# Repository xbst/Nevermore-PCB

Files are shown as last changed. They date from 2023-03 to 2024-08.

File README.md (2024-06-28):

# Nevermore Mini, Max & Stealthmax PCBs
| Nevermore Max 2 PCB | Nevermore Mini & Stealthmax PCB | Nevermore Stealthmax PCB 2|
| --- | --- | --- |
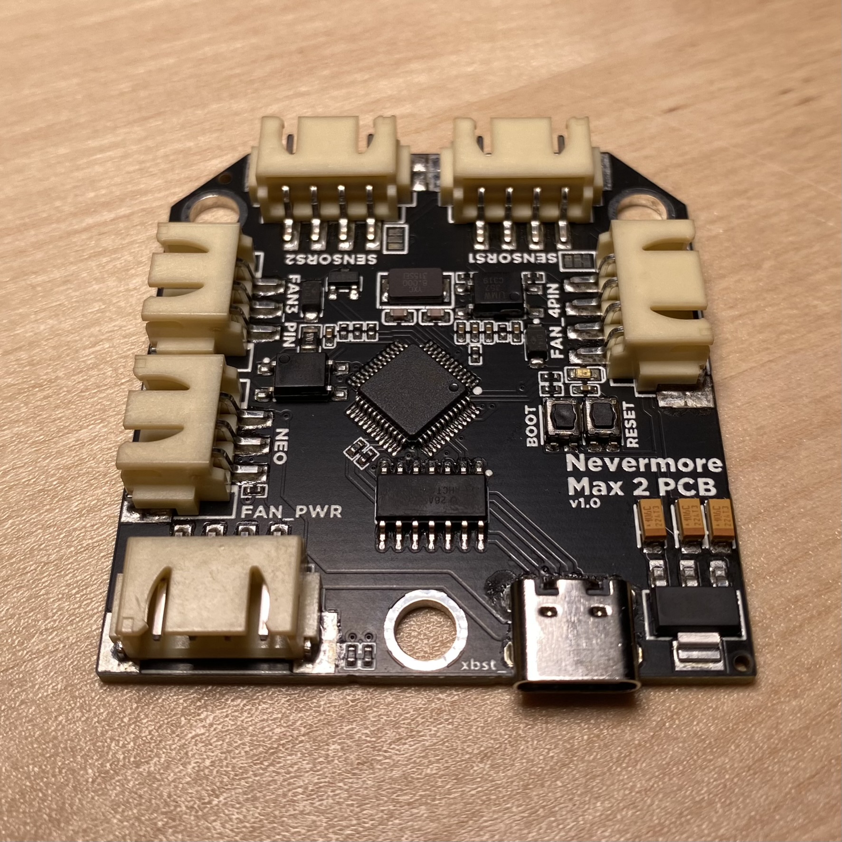
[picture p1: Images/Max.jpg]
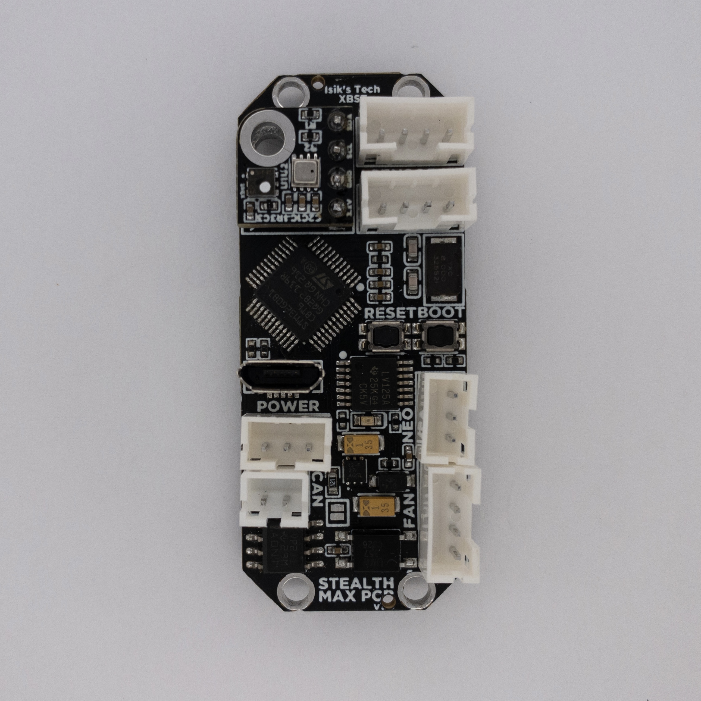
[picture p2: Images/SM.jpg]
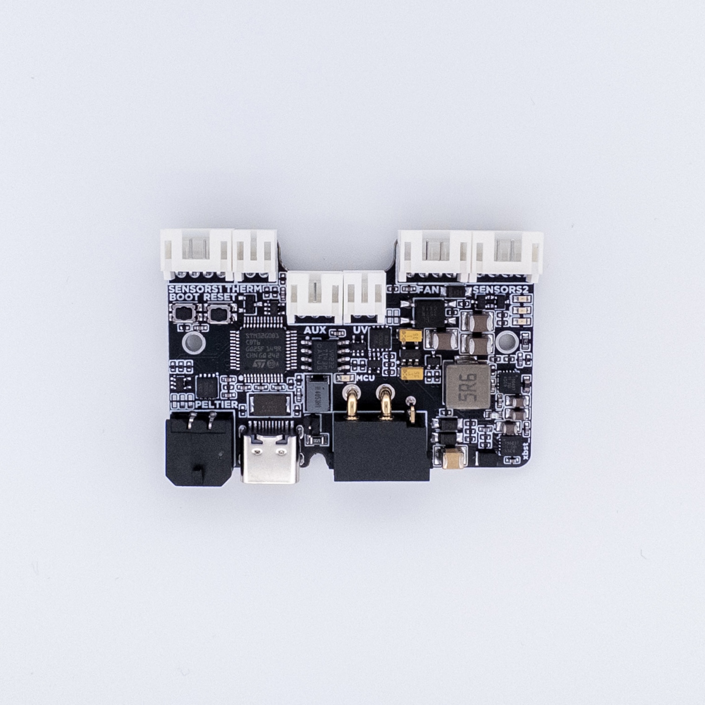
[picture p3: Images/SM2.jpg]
||||

<br>PCBs for Nevermore Mini, Nevermore Max and Nevermore Stealthmax air filters. 
<br>More information about the Nevermore Max 2 air filter can be found [here](https://github.com/nevermore3d/Nevermore_Max)
<br>More information about the Nevermore Stealthmax air filter can be found [here](https://github.com/nevermore3d/StealthMax)
<br>More information about the Nevermore Mini air filter can be found [here](https://www.printables.com/model/757663-nevermore-mini-3d-printer-hepa-and-carbon-air-filt).

### Features
|| Nevermore Max 2 PCB | Nevermore Mini & Stealthmax PCB | Nevermore Stealthmax PCB 2|
|---|---|---|---|
|||||
|MCU|STM32G0B1 MCU|STM32G0B1 MCU|STM32G0B1 MCU|
|Fans|1x 4-pin, 1x 3/2-pin|1x4-pin|1x4-pin|
|Sensors|2x HW I2C|2x HW I2C, 1x Optional Sensor Module Mount|2x HW I2C|
|Neopixels|1x Neopixel|1x Neopixel|-|
|CAN Bus|-|Yes, 1M|Yes, 1M|
|12V Regulator|-|-|Yes, Max. 12V@5A, From 24V|
|5V Regulator|-|-|Yes, From 24V, Turns Off w/ USB to Use USB 5V|
|3.3V Regulator|Yes, From 5V|Yes, From 5V|Yes, From 5V|
|UV LED Control|-|-|1x MOSFET, 1x PWM|
|Peltier Control|-|-|1x MOSFET|
|Thermistors|-|-|1x On-PCB 3950, 1x Connector|
|Connectors|JST-XH, USB C|JST-PH, USB Micro-B|JST-PH, USB C, XT30(2+2), MX3.0 (for Peltier)|

## Purchasing a Nevermore PCB
### United States
|Store|Max|Mini & Stealthmax|Stealthmax 2|
|---|---|---|---|
|Isik's Tech (Me)|[PCB](https://store.isiks.tech/products/nevermore-max-controller-pcb)<br>[Bundle](https://store.isiks.tech/products/nevermore-max-bundle)|[PCB](https://store.isiks.tech/products/nevermore-stealthmax-pxb)<br>[Bundle](https://store.isiks.tech/products/nevermore-stealthmax-bundle)|[PCB](https://store.isiks.tech/products/nevermore-stealthmax-2-pcb)<br>[Bundle](https://store.isiks.tech/products/nevermore-stealthmax-2-bundle)|
|XR Bunker|[PCB](https://xrbunker.works/products/nevermore-max-2-red-pcb-by-xbst_isik)|-|-|

This project is licensed under [GPL v3](./LICENSE), meaning vendors are allowed to sell PCBs without paying me. If you'd like to support the development of this and future projects please consider [sponsoring](https://github.com/sponsors/xbst) me on GitHub. You can also subscribe on [Patreon](https://l.isiks.tech/patreon) or [YouTube](https://l.isiks.tech/member).

You can also use the included gerber files to order your own from a PCB manufacturer like [PCBWay](https://www.pcbway.com/setinvite.aspx?inviteid=374841) or [JLCPCB](https://jlcpcb.com/).
<br>

## Instructions
- [Nevermore Max PCB](./Docs/Max.md)
- [Nevermore Mini & Stealthmax PCB](./Docs/SM.md)
- [Nevermore Stealthmax PCB 2](./Docs/SM2.md)

## YouTube

I am a YouTube content creator. If you want content about these projects & more, please consider [subscribing to my YouTube channel](https://www.youtube.com/channel/UClAWYmCkHjsbaX9Wz1df2mg).
<br>

If you feel like contributing to the development of this project and other projects like this you can sponsor me on [GitHub](https://github.com/sponsors/xbst), subscribe on [Patreon](https://l.isiks.tech/patreon) or [YouTube](https://l.isiks.tech/member).

## Notes
- This readme file contains affiliate links. I make a comission on qualifying purchases.
- This project does not come with any warranty, if you choose to build/use a Nevermore PCB, you are doing this at your own risk!
- If you want to sell PCBs, you are allowed to, and you will not owe me any royalties. **You cannot claim that I endorse the sale**. You can check the license file for more information. However, if you **wish** to give me a share you can sponsor me on [GitHub](https://github.com/sponsors/xbst), subscribe on [Patreon](https://l.isiks.tech/patreon) or [YouTube](https://l.isiks.tech/member).

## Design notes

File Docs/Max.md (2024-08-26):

# Nevermore Max 2 PCB Instructions

## Firmware Flashing

:warning: Do not skip steps 1-6 if you sourced your PCB from anywhere but Isik's Tech. If you do and this setting wasn't pre-applied by the vendor you purchased from, you won't be able to reflash firmware after the initial flash.

1. SSH into your Raspberry Pi.
2. Download the STM32G0 legacy nBOOT_SEL setting file from [its repo](https://github.com/olikraus/stm32g031/tree/main/enable_boot0).  `sudo wget https://raw.githubusercontent.com/olikraus/stm32g031/main/enable_boot0/enable_boot0.hex`
3. Convert the hex file you downloaded to binary. `objcopy --input-target=ihex --output-target=binary enable_boot0.hex enable_boot0.bin`
4. Connect your Nevermore Max PCB to your Raspberry Pi while holding down the `BOOT` button.
5. Use `lsusb` to make sure you can see the device in DFU mode.
6. Flash the binary file to enable legacy nBOOT_SEL mode. `sudo dfu-util -a 0 -d 0483:df11 --dfuse-address 0x08000000:leave -D enable_boot0.bin`
7. Hold down the `BOOT` button on your PCB. While holding it down, press `RESET`, then release `BOOT`. Alternatively, you can unplug the PCB then plug it in again while holding down the `BOOT` button. Use `lsusb` again to make sure you can see the device in DFU mode
8. Go to the Klipper directory. `cd klipper`
9. Clean remaining files from previous build. `make clean`
10. Choose the options for the build. `make menuconfig` Use the following options:
```
[*] Enable extra low-level configuration options
    Micro-controller Architecture (STMicroelectronics STM32)  --->
    Processor model (STM32G0B1)  --->
    Bootloader offset (No bootloader)  --->
    Clock Reference (8 MHz crystal)  --->
    Communication interface (USB (on PA11/PA12))  --->
    USB ids  --->
()  GPIO pins to set at micro-controller startup
```
Press `Q` then `Y` to save and quit the menu.

11. Build. `make`
12. Flash. `make flash FLASH_DEVICE=0483:df11`
13. When finished, press the `RESET` button on your Nevermore Max PCB.
14. Use  `ls /dev/serial/by-id/*` to find the path starting with `/dev/serial/by-id/usb-Klipper_stm32g0b1`. This is the serial path of your Nevermore Max PCB.
15. While you're SSH'd in, also download the python code needed for the SGP40 sensors from the [Nevermore Max repo](https://github.com/nevermore3d/Nevermore_Max).
```
wget https://raw.githubusercontent.com/nevermore3d/Nevermore_Max/master/Software/Klipper/sgp40.py -P ~/klipper/klippy/extras
wget https://raw.githubusercontent.com/nevermore3d/Nevermore_Max/master/Software/Klipper/voc_algorithm.py -P ~/klipper/klippy/extras
systemctl restart klipper
```
16. Run this command if you are using Mainsail and want the SGP40s displayed on the dashboard:
```
cd ~/mainsail/ && grep -l additionalSensors * -R | xargs sed -i 's+additionalSensors=\[+additionalSensors=\["sgp40",+g'
```

## PCB Mount & Wiring
1. Print the ~~bottle opener~~ [Nevermore Max PCB tray](../Mounts/Max/PCB-Tray.stl) using the standard Voron print settings.
2. Remove the built-in supports.
3. Superglue 2 magnets. Pay attention to the polarities.
4. Mount the PCB. The plastic latches will keep the PCB in place, no screws needed. The USB/power side should be seated first.
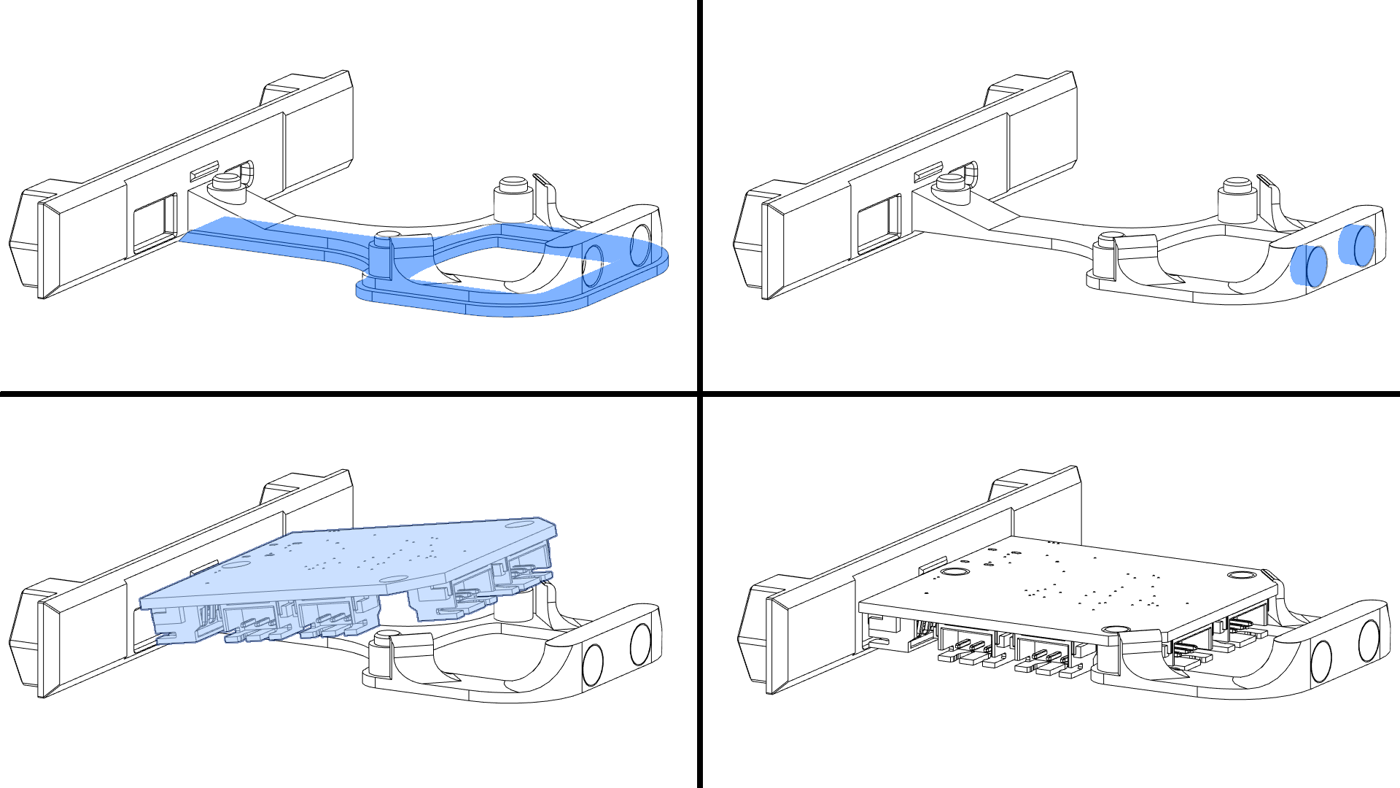
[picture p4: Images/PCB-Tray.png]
Instructions

5. All connectors except USB are JST-XH. Use the diagram below to wire your fans/sensors/leds/power.
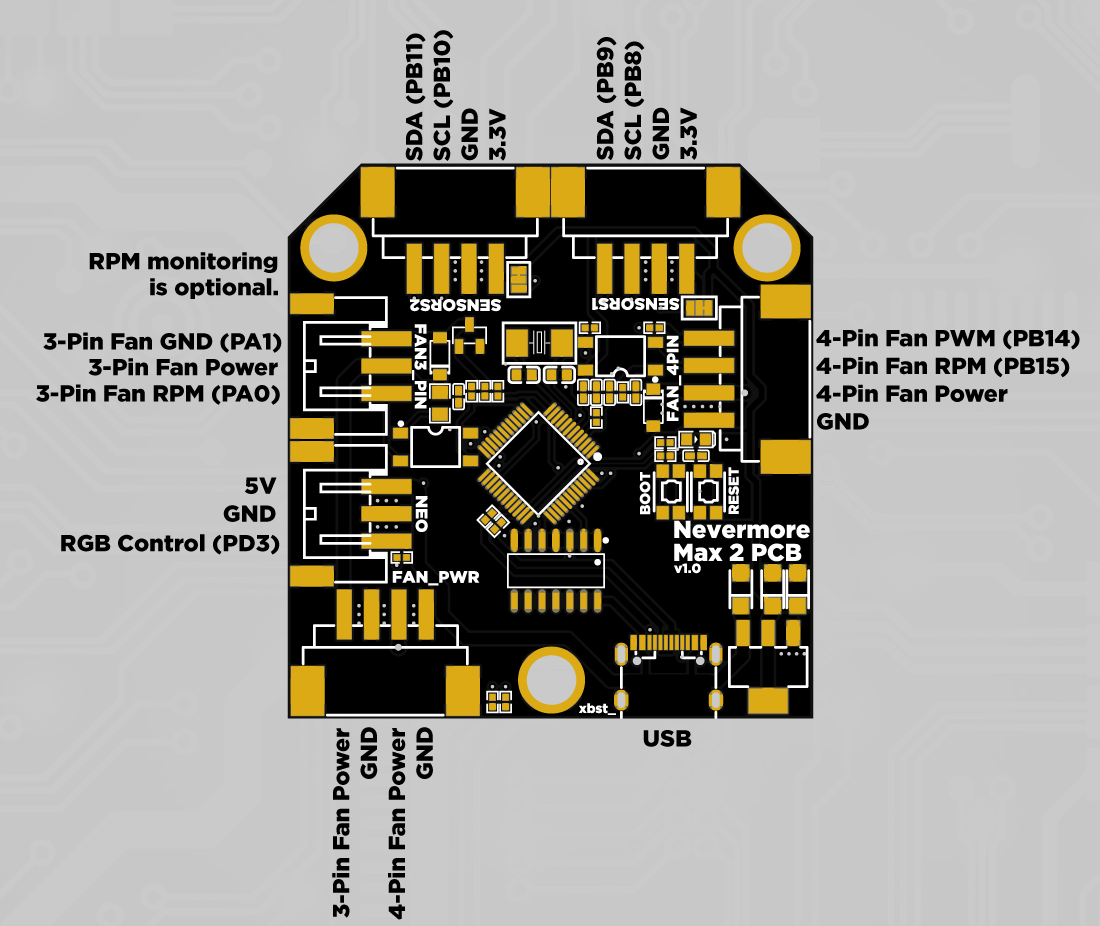
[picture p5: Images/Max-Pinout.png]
Pinout


## Klipper Config
1. Download the [Klipper config](../Firmware/Max.cfg), and upload it to your printer.
2. Open the file and edit according to your setup.
3. Add `[include max.cfg]` in your `printer.cfg`.

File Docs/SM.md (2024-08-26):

# Nevermore Mini And Stealthmax PCB Instructions

## Firmware Flashing

:warning: Do not skip steps 1-6 if you sourced your PCB from anywhere but Isik's Tech. If you do and this setting wasn't pre-applied by the vendor you purchased from, you won't be able to reflash firmware after the initial flash.

1. SSH into your Raspberry Pi.
2. Download the STM32G0 legacy nBOOT_SEL setting file from [its repo](https://github.com/olikraus/stm32g031/tree/main/enable_boot0).  `sudo wget https://raw.githubusercontent.com/olikraus/stm32g031/main/enable_boot0/enable_boot0.hex`
3. Convert the hex file you downloaded to binary. `objcopy --input-target=ihex --output-target=binary enable_boot0.hex enable_boot0.bin`
4. Connect your Nevermore Stealthmax PCB to your Raspberry Pi while holding down the `BOOT` button.
5. Use `lsusb` to make sure you can see the device in DFU mode.
6. Flash the binary file to enable legacy nBOOT_SEL mode. `sudo dfu-util -a 0 -d 0483:df11 --dfuse-address 0x08000000:leave -D enable_boot0.bin`
7. Hold down the `BOOT` button on your PCB. While holding it down, press `RESET`, then release `BOOT`. Alternatively, you can unplug the PCB then plug it in again while holding down the `BOOT` button. Use `lsusb` again to make sure you can see the device in DFU mode
8. Go to the Klipper directory. `cd klipper`
9. Clean remaining files from previous build. `make clean`
10. Choose the options for the build. `make menuconfig` Use the following options:

<details>
  <summary>For USB Serial Communication</summary>

```
[*] Enable extra low-level configuration options
    Micro-controller Architecture (STMicroelectronics STM32)  --->
    Processor model (STM32G0B1)  --->
    Bootloader offset (No bootloader)  --->
    Clock Reference (8 MHz crystal)  --->
    Communication interface (USB (on PA11/PA12))  --->
    USB ids  --->
()  GPIO pins to set at micro-controller startup
```

</details>
<details>
  <summary>For CAN Bus Communication WITHOUT Katapult</summary>

```
[*] Enable extra low-level configuration options
    Micro-controller Architecture (STMicroelectronics STM32)  --->
    Processor model (STM32G0B1)  --->
    Bootloader offset (No bootloader)  --->
    Clock Reference (8 MHz crystal)  --->
    Communication interface (CAN bus (on PB0/PB1))  --->
(1000000) CAN bus speed
()  GPIO pins to set at micro-controller startup
```

</details>
<details>
  <summary>For CAN Bus Communication WITH Katapult</summary>

```
[*] Enable extra low-level configuration options
    Micro-controller Architecture (STMicroelectronics STM32)  --->
    Processor model (STM32G0B1)  --->
    Bootloader offset (8KiB Bootloader)  --->
    Clock Reference (8 MHz crystal)  --->
    Communication interface (CAN bus (on PB0/PB1))  --->
(1000000) CAN bus speed
()  GPIO pins to set at micro-controller startup
```

</details>

Press `Q` then `Y` to save and quit the menu.

11. Build. `make`
12. Flash the firmware. 
<details>
  <summary>For USB Serial Communication</summary>
  
  1. Flash Klipper. `make flash FLASH_DEVICE=0483:df11`
  2. When finished, press the `RESET` button on your Nevermore Stealthmax PCB.
  3. Use  `ls /dev/serial/by-id/*` to find the path starting with `/dev/serial/by-id/usb-Klipper_stm32g0b1`. This is the serial path of your Nevermore Stealthmax PCB.
  
</details>
<details>
  <summary>For CAN Bus Communication WITHOUT Katapult</summary>
  
  1. Flash Klipper. `make flash FLASH_DEVICE=0483:df11`
  2. When finished, press the `RESET` button on your Nevermore Stealthmax PCB.
  3. Use  `~/klippy-env/bin/python ~/klipper/scripts/canbus_query.py can0` to find the CAN bus UUID of your Nevermore Stealthmax PCB. (Make sure your CAN wires are connected.)

</details>
<details>
  <summary>For CAN Bus Communication WITH Katapult</summary>

  1. Go home. `cd ~`
  2. Install [Katapult](https://github.com/Arksine/katapult). `git clone https://github.com/Arksine/katapult`
  3. Go to the Katapult directory. `cd katapult`
  4. Choose the options for the build. `make menuconfig` Use the following options:
    
  ```
    Micro-controller Architecture (STMicroelectronics STM32)  --->
    Processor model (STM32G0B1)  --->
    Build Katapult deployment application (Do not build)  --->
    Clock Reference (8 MHz crystal)  --->
    Communication interface (CAN bus (on PB0/PB1))  --->
    Application start offset (8KiB offset)  --->
(1000000) CAN bus speed
()  GPIO pins to set on bootloader entry
[*] Support bootloader entry on rapid double click of reset button
[ ] Enable bootloader entry on button (or gpio) state
[*] Enable Status LED
(PA13)  Status LED GPIO Pin
  ```
5. Build. `make`
6. Flash Katapult. `sudo dfu-util -a 0 -d 0483:df11 --dfuse-address 0x08000000:leave -D out/canboot.bin`
7. When finished, press the `RESET` button on your Nevermore Stealthmax PCB.
8. Use  `~/klippy-env/bin/python ~/klipper/scripts/canbus_query.py can0` to find the CAN bus UUID of your Nevermore Stealthmax PCB. (Make sure your CAN wires are connected.)
9. Flash Klipper. Replace `<UUID>` with your PCB's UUID. `cd ~/katapult/scripts && python3 flashtool.py -i can0 -f ~/klipper/out/klipper.bin -u <uuid>`
10. When finished, press the `RESET` button on your Nevermore Stealthmax PCB.

</details>

13. While you're SSH'd in, also download the python code needed for the SGP40 sensors from the [Nevermore Max repo](https://github.com/nevermore3d/Nevermore_Max).
```
wget https://raw.githubusercontent.com/nevermore3d/Nevermore_Max/master/Software/Klipper/sgp40.py -P ~/klipper/klippy/extras
wget https://raw.githubusercontent.com/nevermore3d/Nevermore_Max/master/Software/Klipper/voc_algorithm.py -P ~/klipper/klippy/extras
systemctl restart klipper
```
14. Run this command if you are using Mainsail and want the SGP40s displayed on the dashboard:
```
cd ~/mainsail/ && grep -l additionalSensors * -R | xargs sed -i 's+additionalSensors=\[+additionalSensors=\["sgp40",+g'
```

## PCB Mount & Wiring
1. Mount the PCB where the Raspberry Pi Pico normally mounts with M2 screws.
2. All connectors except USB are JST-PH. Use the diagram below to wire your fans/sensors/CAN/power.
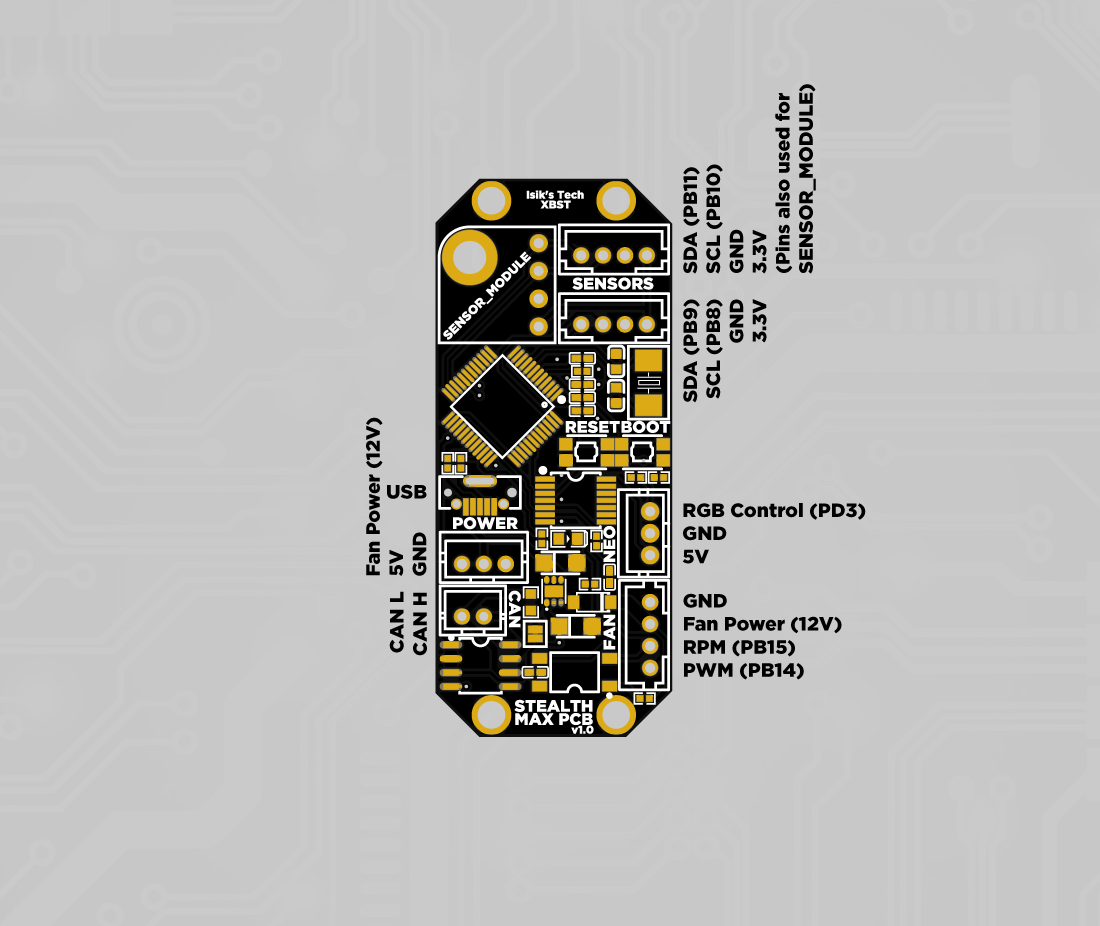
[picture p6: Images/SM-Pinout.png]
Pinout


## Klipper Config
1. Download the [Klipper config](../Firmware/Max.cfg), and upload it to your printer.
2. Open the file and edit according to your setup.
3. Add `[include max.cfg]` in your `printer.cfg`.

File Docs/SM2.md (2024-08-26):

# Nevermore Stealthmax PCB 2 Instructions

## Firmware Flashing

:warning: Do not skip steps 1-6 if you sourced your PCB from anywhere but Isik's Tech. If you do and this setting wasn't pre-applied by the vendor you purchased from, you won't be able to reflash firmware after the initial flash.

1. SSH into your Raspberry Pi.
2. Download the STM32G0 legacy nBOOT_SEL setting file from [its repo](https://github.com/olikraus/stm32g031/tree/main/enable_boot0).  `sudo wget https://raw.githubusercontent.com/olikraus/stm32g031/main/enable_boot0/enable_boot0.hex`
3. Convert the hex file you downloaded to binary. `objcopy --input-target=ihex --output-target=binary enable_boot0.hex enable_boot0.bin`
4. Connect your Nevermore Stealthmax PCB to your Raspberry Pi while holding down the `BOOT` button.
5. Use `lsusb` to make sure you can see the device in DFU mode.
6. Flash the binary file to enable legacy nBOOT_SEL mode. `sudo dfu-util -a 0 -d 0483:df11 --dfuse-address 0x08000000:leave -D enable_boot0.bin`
7. Hold down the `BOOT` button on your PCB. While holding it down, press `RESET`, then release `BOOT`. Alternatively, you can unplug the PCB then plug it in again while holding down the `BOOT` button. Use `lsusb` again to make sure you can see the device in DFU mode
8. Go to the Klipper directory. `cd klipper`
9. Clean remaining files from previous build. `make clean`
10. Choose the options for the build. `make menuconfig` Use the following options:

<details>
  <summary>For USB Serial Communication</summary>

```
[*] Enable extra low-level configuration options
    Micro-controller Architecture (STMicroelectronics STM32)  --->
    Processor model (STM32G0B1)  --->
    Bootloader offset (No bootloader)  --->
    Clock Reference (8 MHz crystal)  --->
    Communication interface (USB (on PA11/PA12))  --->
    USB ids  --->
()  GPIO pins to set at micro-controller startup
```

</details>
<details>
  <summary>For CAN Bus Communication WITHOUT Katapult</summary>

```
[*] Enable extra low-level configuration options
    Micro-controller Architecture (STMicroelectronics STM32)  --->
    Processor model (STM32G0B1)  --->
    Bootloader offset (No bootloader)  --->
    Clock Reference (8 MHz crystal)  --->
    Communication interface (CAN bus (on PB0/PB1))  --->
(1000000) CAN bus speed
()  GPIO pins to set at micro-controller startup
```

</details>
<details>
  <summary>For CAN Bus Communication WITH Katapult</summary>

```
[*] Enable extra low-level configuration options
    Micro-controller Architecture (STMicroelectronics STM32)  --->
    Processor model (STM32G0B1)  --->
    Bootloader offset (8KiB Bootloader)  --->
    Clock Reference (8 MHz crystal)  --->
    Communication interface (CAN bus (on PB0/PB1))  --->
(1000000) CAN bus speed
()  GPIO pins to set at micro-controller startup
```

</details>

Press `Q` then `Y` to save and quit the menu.

11. Build. `make`
12. Flash the firmware. 
<details>
  <summary>For USB Serial Communication</summary>
  
  1. Flash Klipper. `make flash FLASH_DEVICE=0483:df11`
  2. When finished, press the `RESET` button on your Nevermore Stealthmax PCB.
  3. Use  `ls /dev/serial/by-id/*` to find the path starting with `/dev/serial/by-id/usb-Klipper_stm32g0b1`. This is the serial path of your Nevermore Stealthmax PCB.
  
</details>
<details>
  <summary>For CAN Bus Communication WITHOUT Katapult</summary>
  
  1. Flash Klipper. `make flash FLASH_DEVICE=0483:df11`
  2. When finished, press the `RESET` button on your Nevermore Stealthmax PCB.
  3. Use  `~/klippy-env/bin/python ~/klipper/scripts/canbus_query.py can0` to find the CAN bus UUID of your Nevermore Stealthmax PCB. (Make sure your CAN wires are connected.)

</details>
<details>
  <summary>For CAN Bus Communication WITH Katapult</summary>

  1. Go home. `cd ~`
  2. Install [Katapult](https://github.com/Arksine/katapult). `git clone https://github.com/Arksine/katapult`
  3. Go to the Katapult directory. `cd katapult`
  4. Choose the options for the build. `make menuconfig` Use the following options:
    
  ```
    Micro-controller Architecture (STMicroelectronics STM32)  --->
    Processor model (STM32G0B1)  --->
    Build Katapult deployment application (Do not build)  --->
    Clock Reference (8 MHz crystal)  --->
    Communication interface (CAN bus (on PB0/PB1))  --->
    Application start offset (8KiB offset)  --->
(1000000) CAN bus speed
()  GPIO pins to set on bootloader entry
[*] Support bootloader entry on rapid double click of reset button
[ ] Enable bootloader entry on button (or gpio) state
[*] Enable Status LED
(PA13)  Status LED GPIO Pin
  ```
5. Build. `make`
6. Flash Katapult. `sudo dfu-util -a 0 -d 0483:df11 --dfuse-address 0x08000000:leave -D out/canboot.bin`
7. When finished, press the `RESET` button on your Nevermore Stealthmax PCB.
8. Use  `~/klippy-env/bin/python ~/klipper/scripts/canbus_query.py can0` to find the CAN bus UUID of your Nevermore Stealthmax PCB. (Make sure your CAN wires are connected.)
9. Flash Klipper. Replace `<UUID>` with your PCB's UUID. `cd ~/katapult/scripts && python3 flashtool.py -i can0 -f ~/klipper/out/klipper.bin -u <uuid>`
10. When finished, press the `RESET` button on your Nevermore Stealthmax PCB.

</details>

13. While you're SSH'd in, also download the python code needed for the SGP40 sensors from the [Nevermore Max repo](https://github.com/nevermore3d/Nevermore_Max).
```
wget https://raw.githubusercontent.com/nevermore3d/Nevermore_Max/master/Software/Klipper/sgp40.py -P ~/klipper/klippy/extras
wget https://raw.githubusercontent.com/nevermore3d/Nevermore_Max/master/Software/Klipper/voc_algorithm.py -P ~/klipper/klippy/extras
systemctl restart klipper
```
14. Run this command if you are using Mainsail and want the SGP40s displayed on the dashboard:
```
cd ~/mainsail/ && grep -l additionalSensors * -R | xargs sed -i 's+additionalSensors=\[+additionalSensors=\["sgp40",+g'
```
## PCB Mount & Wiring
1. Download and print the necessary files from this repo. You'll need to at least print the "Spacer" for your printer size. You can use the stock latch with the Rasperry Pi logo, or download the version from this repo with the Isik's Tech logo.

|Filter |Spacer|Latch|
|---|---|-----|
|Stealthmax  |[Spacer](../Mounts/Stealthmax/Spacer.stl)|[Latch](../Mounts/Stealthmax/Latch.stl)|
|Stealthmax S|[Spacer](../Mounts/Stealthmax-S/Spacer.stl)|[Latch](../Mounts/Stealthmax-S/Latch.stl)|

2. Place the spacer over the screw holes of the electronics chamber of your filter. The top side of the mount (printing orientation), faces down. Align the outer screw holes with the holes on the spacer.
3. Attach the heatsink to the PCB, behind the corner with the buck converters. Align its edges with the edges of the PCB. This is where it fits with the spacer:
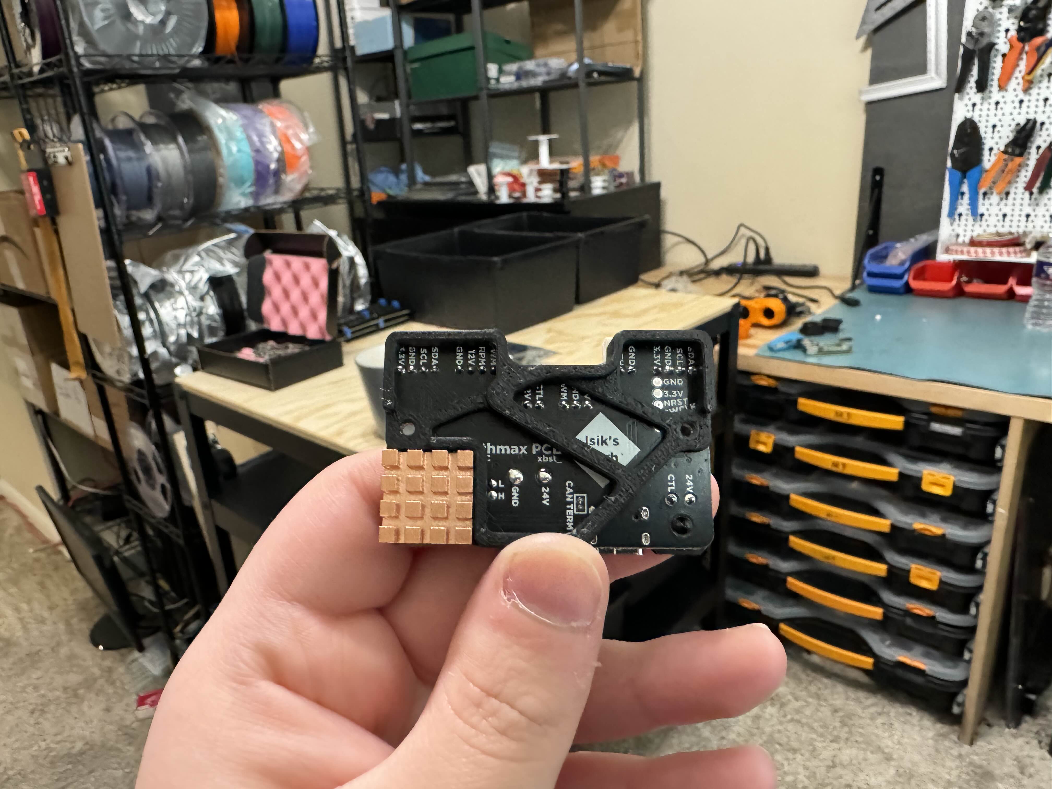
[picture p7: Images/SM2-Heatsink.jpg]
Heatsink

4. Do the wiring. All internal connectors except peltier are JST-PH, peltier is MX3.0. CAN/VIN connector is XT30(2+2). Use the diagram below to wire your fan/sensors/leds/thermistor/peltier.
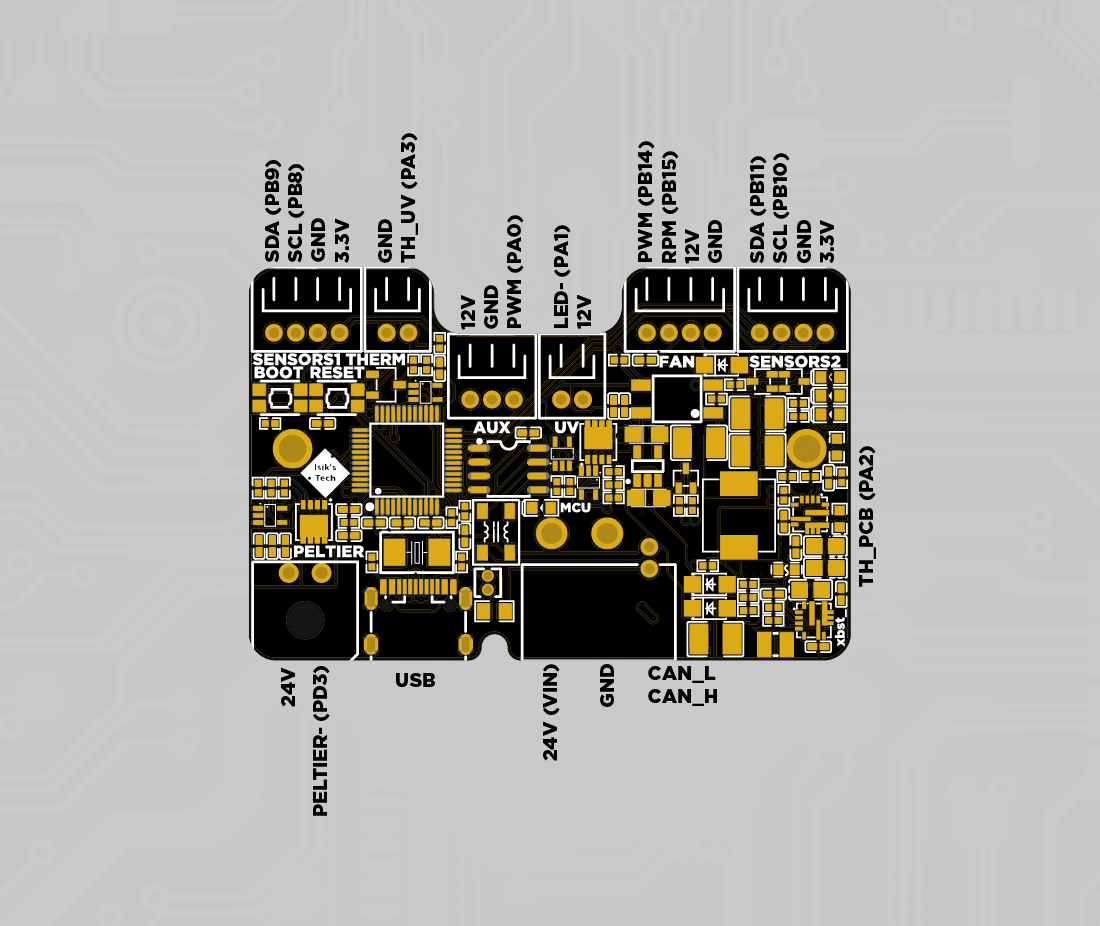
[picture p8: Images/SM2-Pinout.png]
Pinout


## Klipper Config
1. Download the [Klipper config](../Firmware/SM2.cfg), and upload it to your printer.
2. Open the file and edit according to your setup.
3. Add `[include SM2.cfg]` in your `printer.cfg`.

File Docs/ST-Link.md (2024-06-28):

# ST-Link Instructions
If you cannot enter DFU mode by holding down the BOOT button, your PCB might be "bricked". Fortunately, it is possible to reverse this.
## Tools
### 1. ST-Link
|Source|Link|
|---|----|
|Amazon US|[Link](https://amzn.to/474WZEU)|
|Aliexpress|[Link](https://s.click.aliexpress.com/e/_DluRpA7)|
### 2. Dupont Wires
Your ST-Link might come with some in the package. If it doesn't:
|Source|Link|
|---|----|
|Amazon US|[Link](https://amzn.to/3SClTaO)|
|Aliexpress|[Link](https://s.click.aliexpress.com/e/_DDWGigj)|
### 3. Soldering Supplies
You'll need to solder some male dupont wires on the PCB, so you need a soldering iron and solder.
## Instructions
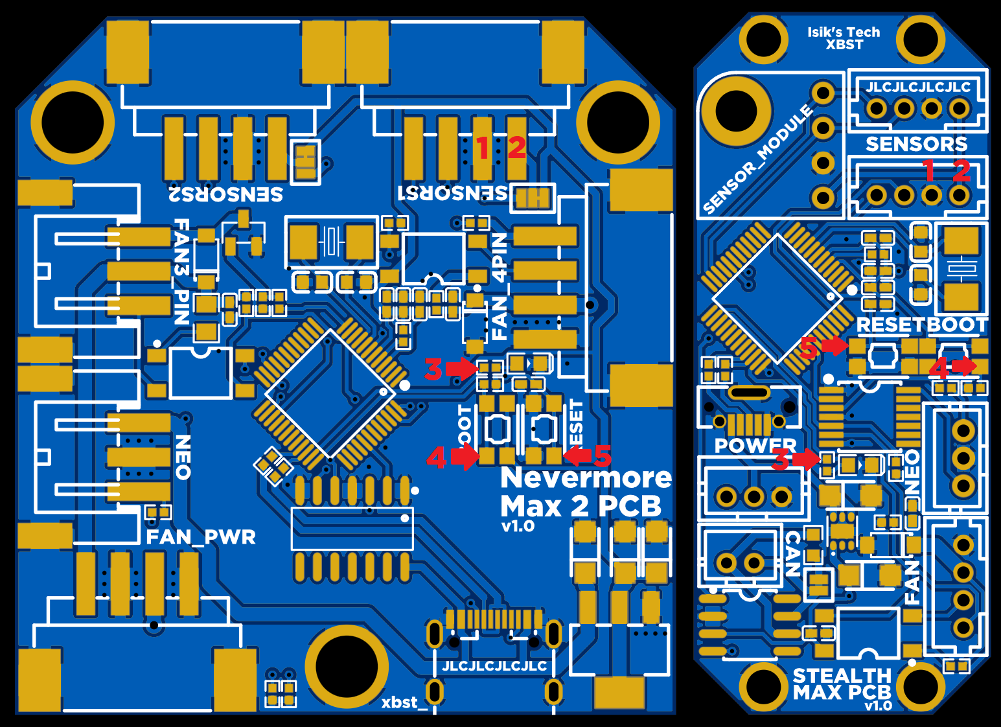
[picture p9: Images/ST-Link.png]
ST-Link Pads


Connect your ST-Link wires to the pads highlighted above. If you have a Stealthmax PCB 2, the pads are on the backside, labeled.
| Pin | ST-Link |
|-----|---|
|1 |GND |
|2 |3.3V |
|3 |SWDIO |
|4 |SWCLK |
|5 |RST |

1. SSH into your Raspberry Pi
2. Install the software St-Link needs: ```sudo apt install cmake libusb-1.0-0-dev```
3. Download the ST-Link tools from GitHub: ```git clone https://github.com/stlink-org/stlink ~/stlink```
4. Go to the newly created stlink directory: ```cd ~/stlink```
5. Make: ```make release```
6. Copy the chip info to /usr: ```sudo cp -a ~/stlink/config/chips /usr/local/share/stlink```
7. Plug in the ST-Link
8. Test the connection: ```sudo st-flash --area=option read``` If you DON'T see a `unknown chip id` error, you can move on to the next step.
9. Reset the nBOOT_SEL setting: ```sudo ./build/Release/bin/st-flash --connect-under-reset --area=option write 0xfedffeaa```
10. If there were no errors, you should be able to enter DFU mode now. Unsolder all wires, connect your PCB while holding the BOOT button down. You should be able to see your PCB in DFU mode. You can use `lsusb` to see if it's in DFU mode.

## Notes
- This readme file contains affiliate links. I earn a comission on qualifying purchases.

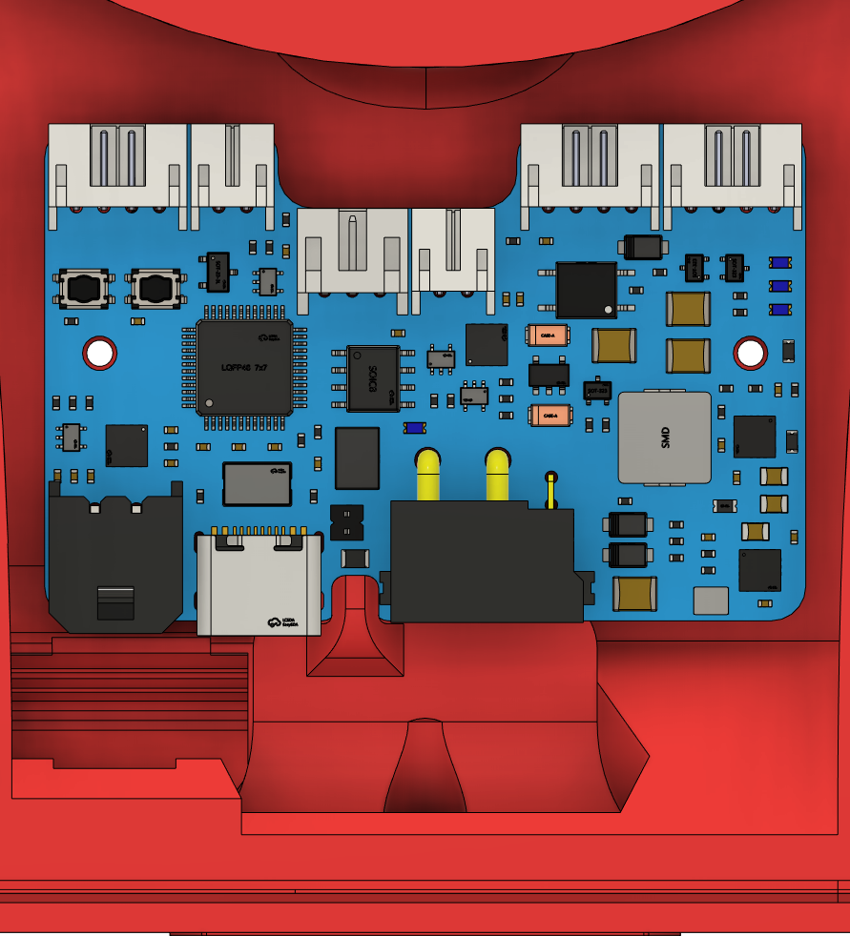
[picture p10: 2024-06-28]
Images/SM2-Cap.png

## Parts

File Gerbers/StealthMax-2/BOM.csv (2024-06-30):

ID | Name | Designator | Footprint | Quantity | Manufacturer Part | Manufacturer | Supplier | Supplier Part | Price
1 | NP | C30,C3,C12,C31,C32 | C0402 | 5 | NOT POPULATED |  |  | NOT POPULATED
2 | SS24L | D3,D1,D2 | SOD-123FL_L2.8-W1.8-LS3.7-R-RD | 3 | SS24L | Hottech(合科泰) | LCSC | C2827931 | 0.022
3 | 3.3uH | L1 | IND-SMD_L2.5-W2.0 | 1 | FTC252012S3R3MBCA | cjiang(长江微电) | LCSC | C5832373 | 0.081
4 | 2N7002W | Q5,Q3,Q4 | SOT-323-3_L2.0-W1.3-P1.30-LS2.1-BR | 3 | 2N7002W | 宏迦橙 | LCSC | C7420322 | 0.015
5 | 0Ω | R34,R37,R20,R14 | R0402 | 4 | 0402WGF0000TCE | UNI-ROYAL(厚声) | LCSC | C17168 | 0.001
6 | 10kΩ | R36,R29,R32,R1,R6,R12,R21 | R0402 | 7 | 0402WGF1002TCE | UNI-ROYAL(厚声) | LCSC | C25744 | 0.001
7 | SN74AHCT1G125DCKR | U8,U9,U3,U10 | SC-70-5_L2.0-W1.3-P0.65-LS2.1-BL | 4 | SN74AHCT1G125DCKR | TI(德州仪器) | LCSC | C350557 | 0.079
8 | WSD3066DN33 | Q1,Q2 | DFN-8_L3.3-W3.3-P0.65-BL | 2 | WSD3066DN33 | WINSOK(微硕) | LCSC | C148386 | 0.275
9 | 10Ω | R5,R8,R11 | R0402 | 3 | 0402WGF100JTCE | UNI-ROYAL(厚声) | LCSC | C25077 | 0.001
10 | 1.5kΩ | R7,R16,R26,R13 | R0402 | 4 | 0402WGF1501TCE | UNI-ROYAL(厚声) | LCSC | C25867 | 0.001
11 | LED-0603_B | 3V3,5V,12V,MCU | LED0603_BLUE | 4 | 19-217/BHC-ZL1M2RY/3T | EVERLIGHT(台湾亿光) | LCSC | C72041 | 0.021
12 | XT30(2+2)PW-M.G.B | CAN+VIN | XT30(2+2)_NO_TAB | 1 | XT30(2+2)PW-M.G.B | AMASS(艾迈斯) | LCSC | C19268030 | 0.505
13 | 1uF | C2,C11 | CASE-A_3216 | 2 | CA45-A-35V-1uF-K | CEC(振华新云) | LCSC | C141744 | 0.084
14 | AP2112K-3.3TRG1 | U1 | SOT-25-5_L2.9-W1.6-P0.95-LS2.8-BL | 1 | AP2112K-3.3TRG1 | DIODES(美台) | LCSC | C51118 | 0.076
15 | 47uF | C1 | C1210 | 1 | GRM32ER61C476KE15L | muRata(村田) | LCSC | C77101 | 0.127
16 | 100nF | C13,C14,C27,C4,C18,C19,C22,C5,C6,C7,C10 | C0402 | 11 | 0402B104K500NT | FH(风华) | LCSC | C110251 | 0.002
17 | 10uF | C15,C16,C17 | C0805 | 3 | GRM21BR61H106KE43L | muRata(村田) | LCSC | C440198 | 0.066
18 | 100pF | C23,C20 | C0402 | 2 | C1005C0G1H101JT000F | TDK | LCSC | C445763 | 0.01
19 | F0603HI8000V032TM | F1 | F0603 | 1 | F0603HI8000V032TM | AEM | LCSC | C310942 | 0.062
20 | 73.2kΩ | R30 | R0402 | 1 | RC0402FR-0773K2L | YAGEO(国巨) | LCSC | C185398 | 0.001
21 | 20kΩ | R33,R4,R10,R15,R31 | R0402 | 5 | 0402WGF2002TCE | UNI-ROYAL(厚声) | LCSC | C25765 | 0.001
22 | 100kΩ | R35,R18 | R0402 | 2 | 0402WGF1003TCE | UNI-ROYAL(厚声) | LCSC | C25741 | 0.001
23 | TPS56637RPAR | U5,U7 | VQFN-HR-10_L3.0-W3.0_RPA | 2 | TPS56637RPAR | TI(德州仪器) | LCSC | C841386 | 1.283
24 | HC-MX3.0-2AW | PELTIER | CONN-TH_2P-P3.00_MOLEX_436500200 | 1 | HC-MX3.0-2AW | HCTL | LCSC | C5441111 | 0.086
25 | 120Ω | R3 | R0805 | 1 | ERJP06F1200V | PANASONIC(松下) | LCSC | C543533 | 0.02
26 | SN65HVD232DR | U6 | SOIC-8_L5.0-W4.0-P1.27-LS6.0-BL | 1 | SN65HVD232DR | TI(德州仪器) | LCSC | C30530 | 0.577
27 | 1.27MM/1*2P | CAN_TERM | HDR-TH_2P-P1.27-V-M | 1 | 1.27-1*2P针 | BOOMELE(博穆精密) | LCSC | C703015 | 0.016
28 | ACT45C-101-2P-TL-000 | L3 | FILTER-SMD_4P-L4.5-W3.2-BL_ACT45C-101-2P-TL-000 | 1 | ACT45C-101-2P-TL000 | TDK | LCSC | C404371 | 0.382
29 | PH-3AWD | AUX | CONN-TH_3P-P2.00_PH-3AWD | 1 | PH-3AWD | BOOMELE(博穆精密) | LCSC | C49993 | 0.013
30 | 22uF | C21,C25,C26 | C1210 | 3 | C3225X7R1C226MT000N | TDK | LCSC | C342699 | 0.2
31 | 5.6uH | L2 | IND-SMD_L7.1-W6.6 | 1 | YSPI0630A-5R6M | YJYCOIN(益嘉源) | LCSC | C497868 | 0.113
32 | 383kΩ | R28 | R0603 | 1 | RS-03K3833FT | FH(风华) | LCSC | C294660 | 0.001
33 | 30pF | C8,C9 | C0402 | 2 | 0402CG300J500NT | FH(风华) | LCSC | C1570 | 0.001
34 | 2.2uF | C24 | C0402 | 1 | CL05A225MQ5NSNC | SAMSUNG(三星) | LCSC | C12530 | 0.002
35 | BAV99,215 | D4 | SOT-23-3_L2.9-W1.6-P1.90-LS2.8-BR | 1 | BAV99,215 | Nexperia(安世) | LCSC | C2500 | 0.009
36 | 5.1kΩ | R17,R19 | R0402 | 2 | 0402WGF5101TCE | UNI-ROYAL(厚声) | LCSC | C25905 | 0.001
37 | 4.7kΩ | R22,R27,R2,R9 | R0402 | 4 | 0402WGF4701TCE | UNI-ROYAL(厚声) | LCSC | C25900 | 0.001
38 | 2.37K | R23,R24 | R0402 | 2 | RC0402FR-072K37L | YAGEO(国巨) | LCSC | C294439
39 | SDNT1608X104F3950FTF | R25 | R0603 | 1 | SDNT1608X104F3950FTF | Sunlord(顺络) | LCSC | C919169 | 0.02
40 | PH-2AWD | THERM,UV | CONN-TH_PH-2AW | 2 | PH-2AWD | BOOMELE(博穆精密) | LCSC | C49992 | 0.009
41 | EL357N(C)(TA)-G | U4 | OPTO-SMD-4_L4.4-W4.1-P2.54-LS7.0-TL | 1 | EL357N(C)(TA)-G | EVERLIGHT(亿光) | LCSC | C29981 | 0.055
42 | 8MHz | X1 | CRYSTAL-SMD_L5.0-W3.2 | 1 | X50328MSB2GI | YXC(扬兴晶振) | LCSC | C115962 | 0.189
43 | PH-4AWD | SENSORS2,SENSORS1,FAN | CONN-TH_PH-4AWD | 3 | PH-4AWD | BOOMELE(博穆精密) | LCSC | C49994 | 0.017
44 | EVPAA202K | BOOT,RESET | KEY-SMD_4P-L3.5-W2.9-P1.48-LS4.3-TL | 2 | EVPAA202K | PANASONIC(松下) | LCSC | C79147 | 0.327
45 | STM32G0B1CBT6 | U2 | LQFP-48_L7.0-W7.0-P0.50-LS9.0-BL | 1 | STM32G0B1CBT6 | ST(意法半导体) | LCSC | C2847904 | 1.809
46 | USB3.1C16PFSMT | USBC | USB-C-SMD_TYPE-C-USB-17 | 1 | - | LCSC | LCSC | C167321 | 0.35
47 | NO | 3.3V,GND,NRST,SWCLK,SWDIO | TP | 5

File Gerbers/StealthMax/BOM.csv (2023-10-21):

ID | Name | Designator | Footprint | Quantity | Manufacturer Part | Manufacturer | Supplier | Supplier Part | Price
1 | 4.7kΩ | R2,R9 | R0402 | 2 | 0402WGF4701TCE | UNI-ROYAL(厚声) | LCSC | C25900 | 0.001
2 | _ | SENSOR_MODULE |  | 1
3 | B2B-PH-KL | CAN | CONN-TH_2P-P2.00_2B-PH-KL | 1 |  | JST | LCSC | C2683610 | 0.062
4 | B4B-PH-K-S-(LF)(SN) | FAN,SENSORS,SENSORS2 | CONN-TH_B4B-PH-K-S-LF-SN | 3 |  | JST Sales America | LCSC | C160257 | 0.059
5 | 470R 1% | R10 | R0402 | 1 |  |  | LCSC | C25117 | 0.001
6 | SN74LV125APWR_C406868 | U3 | TSSOP-14_L5.0-W4.4-P0.65-LS6.4-BL | 1 |  | TI(德州仪器) | LCSC | C406868 | 0.207
7 | PH-3A_C722771 | NEO,POWER | CONN-TH_PH-3A | 2 |  | CAX(创都) | LCSC | C722771 | 0.006
8 | 10K 1% | R6,R1 | R0402 | 2 |  |  | LCSC | C25744 | 0.001
9 | STM32G0B1CBT6 | U2 | LQFP-48_L7.0-W7.0-P0.50-LS9.0-BL | 1 | STM32G0B1CBT6 | ST(意法半导体) | LCSC | C2847904 | 3.131
10 | EVPAA202K | BOOT,RESET | KEY-SMD_4P-L3.5-W2.9-P1.48-LS4.3-TL | 2 | EVPAA202K | PANASONIC(松下) | LCSC | C79147 | 0.356
11 | 100n | C4,C5,C7,C10,C18,C23 | C0402 | 6 |  |  | LCSC | C1525 | 0.001
12 | 30pF | C8,C9 | C0603 | 2 | 0603CG300J500NT | FH(风华) | LCSC | C1658 | 0.003
13 | DSS14 | D1 | SOD-123_L2.8-W1.8-LS3.7-RD | 1 | DSS14 | STARSEA | LCSC | C59293 | 0.026
14 | LED-0603_B | LED1 | LED0603_BLUE | 1 | 19-217/BHC-ZL1M2RY/3T | EVERLIGHT(台湾亿光) | LCSC | C72041 | 0.018
15 | 27R4 1% | R3,R4 | R0402 | 2 |  |  | LCSC | C31439 | 0.001
16 | 10Ω | R5 | R0402 | 1 | 0402WGF100JTCE | UNI-ROYAL(厚声) | LCSC | C25077 | 0.001
17 | 1.5kΩ | R13 | R0402 | 1 | 0402WGF1501TCE | UNI-ROYAL(厚声) | LCSC | C25867 | 0.001
18 | 120Ω | R14 | R0603 | 1 | WR06X121JTL | Walsin(华新科) | LCSC | C163857 | 0.001
19 | EL357C | U4 | SOP-4_L3.6-W4.4-P2.54-LS7.0-TL | 1 | EL357C | UMW(广东友台半导体) | LCSC | C725794 | 0.055
20 | SN65HVD232DR | U6 | SOIC-8_L5.0-W4.0-P1.27-LS6.0-BL | 1 | SN65HVD232DR | TI(德州仪器) | LCSC | C30530 | 1.021
21 | U-E-051N-4BH21-F1B | USB | MICRO-USB-SMD_U-E-051N-4BH21-F1B | 1 | U-E-051N-4BH21-S1B | XKB Connectivity(中国星坤) | LCSC | C319153 | 0.21
22 | 8MHz | X1 | CRYSTAL-SMD_L5.0-W3.2 | 1 | X50328MSB2GI | YXC(扬兴晶振) | LCSC | C115962 | 0.182
23 | 1u | C1,C2 | CAP-SMD_L3.2-W1.6-R-RD | 2 |  |  | LCSC | C141744 | 0.089
24 | LP5912-3.3DRVR | U1 | WSON-6_L2.0-W2.0-P0.65-TL-EP | 1 | LP5912-3.3DRVR | TI(德州仪器) | LCSC | C524780 | 0.773

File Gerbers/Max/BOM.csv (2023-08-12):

ID | Name | Designator | Footprint | Quantity | Manufacturer Part | Manufacturer | Supplier | Supplier Part | Price
1 | STM32G0B1CBT6 | U2 | LQFP-48_L7.0-W7.0-P0.50-LS9.0-BL | 1 | STM32G0B1CBT6 | ST(意法半导体) | LCSC | C2847904 | 3.196
2 | SN74AHCT125DR | U6 | SOIC-14_L8.7-W3.9-P1.27-LS6.0-BL | 1 | SN74AHCT125DR | TI(德州仪器) | LCSC | C155176 | 0.225
3 | 100n | C5,C7,C10,C23,C6,C18 | C0402 | 6 |  |  | LCSC | C1525 | 0.001
4 | 1.5kΩ | R13 | R0402 | 1 | 0402WGF1501TCE | UNI-ROYAL(厚声) | LCSC | C25867 | 0.001
5 | LED-0603_B | LED1 | LED0603_BLUE | 1 | 19-217/BHC-ZL1M2RY/3T | EVERLIGHT(台湾亿光) | LCSC | C72041 | 0.018
6 | EVPAA202K | BOOT,RESET | KEY-SMD_4P-L3.5-W2.9-P1.48-LS4.3-TL | 2 | EVPAA202K | PANASONIC(松下) | LCSC | C79147 | 0.356
7 | 10K 1% | R1,R16 | R0402 | 2 |  |  | LCSC | C25744 | 0.001
8 | 10Ω | R5 | R0402 | 1 | 0402WGF100JTCE | UNI-ROYAL(厚声) | LCSC | C25077 | 0.001
9 | 30pF | C8,C9 | C0603 | 2 | 0603CG300J500NT | FH(风华) | LCSC | C1658 | 0.004
10 | 4.7kΩ | R2,R9,R11 | R0402 | 3 | 0402WGF4701TCE | UNI-ROYAL(厚声) | LCSC | C25900 | 0.001
11 | 4.7kΩ | R12 | R0805 | 1 | 0805W8F4701T5E | UNI-ROYAL(厚声) | LCSC | C17673 | 0.002
12 | EL357C | U4,U5 | SOP-4_L3.6-W4.4-P2.54-LS7.0-TL | 2 | EL357C | UMW(广东友台半导体) | LCSC | C725794 | 0.055
13 | 8MHz | X1 | CRYSTAL-SMD_L5.0-W3.2 | 1 | X50328MSB2GI | YXC(扬兴晶振) | LCSC | C115962 | 0.174
14 | DSS14 | D1,D6 | SOD-123_L2.8-W1.8-LS3.7-RD | 2 | DSS14 | STARSEA | LCSC | C59293 | 0.026
15 | S3B-XH-SM4-TB (LF)(SN) | FAN3_PIN,NEO | CONN-TH_S3B-XH-SM4-TB-LF-SN | 2 | - | JST Sales America | LCSC | C161860 | 0.382
16 | IRLML6344GT | Q1 | SOT-23-3_L2.9-W1.3-P1.90-LS2.4-BR | 1 | SK2304AA | Shikues | LCSC | C130871 | 0.053
17 | 100R 1% | R15 | R0402 | 1 |  |  | LCSC | C25076 | 0.001
18 | 470R 1% | R10,R8 | R0402 | 2 |  |  | LCSC | C25117 | 0.001
19 | 5K1 1% | R7,R6 | R0402 | 2 |  |  | LCSC
20 | 27R4 1% | R4,R3 | R0402 | 2 |  |  | LCSC | C31439 | 0.001
21 | S4B-XH-SM4-TB-(LF)(SN) | FAN_PWR,SENSORS2,FAN_4PIN,SENSORS1 | CONN-SMD_S4B-XH-SM4-TB-LF-SN | 4 | S4B-XH-SM4-TB-(LF)(SN) | JST Sales America | LCSC | C161861 | 0.409
22 | USB3.1C16PFSMT | USBC | USB-C-SMD_TYPE-C-USB-17 | 1 | - | LCSC | LCSC | C167321 | 0.358
23 | AMS1117-3.3 | U1 | SOT-223-3_L6.5-W3.4-P2.30-LS7.0-BR | 1 | AMS1117-3.3 | AMS | LCSC | C6186 | 0.142
24 | 10u | C3,C2,C1 | CAP-SMD_L3.2-W1.6-R-RD | 3 | TAJA106K016RNJ | AVX | LCSC | C7171 | 0.097

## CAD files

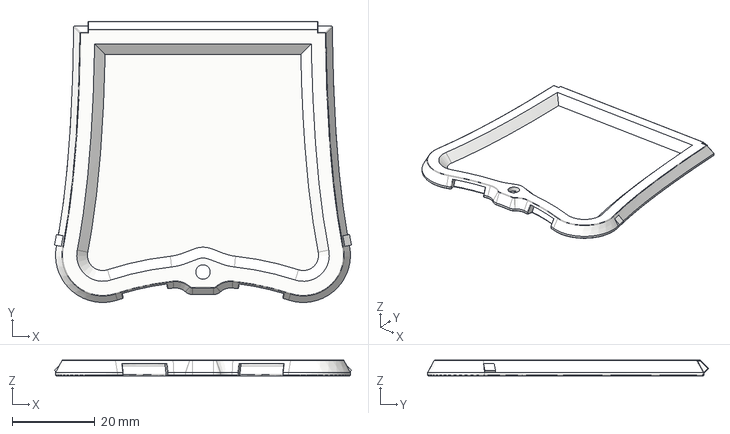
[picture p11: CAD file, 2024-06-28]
CAD/Stealthmax-Latch.step
71.7 x 67.8 x 3.80 mm

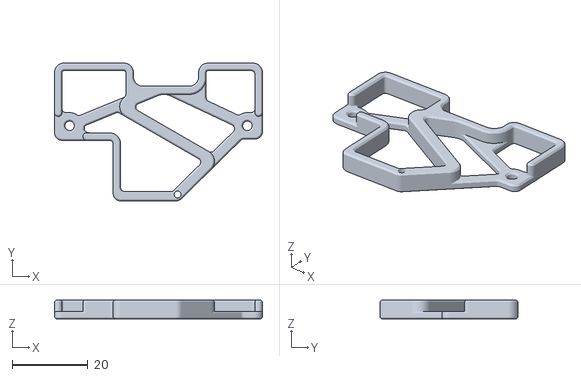
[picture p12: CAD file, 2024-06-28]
Mounts/Stealthmax-S/Spacer.stl
55.0 x 36.4 x 5.00

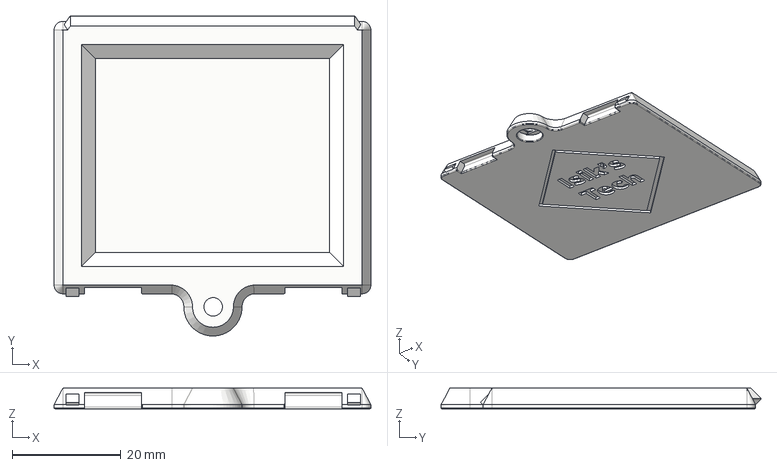
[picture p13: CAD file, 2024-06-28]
CAD/Stealthmax-S-Latch.step
58.2 x 58.8 x 3.80 mm

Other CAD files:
Mounts/Stealthmax-S/Latch.stl

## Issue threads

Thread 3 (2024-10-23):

navermorepcbmax2

elizabeth-4, 2024-10-23:

xbst, 2024-10-23:
Ignore `dfu-util: Error during download get_status`
`File downloaded successfully` means it flashed successfully.

elizabeth-4, 2024-10-24:
But it won't let me flash klipper

make flash FLASH_DEVICE=0483:df11
  Flashing out/klipper.bin to 0483:df11
sudo dfu-util -d ,0483:df11 -R -a 0 -s 0x8000000:leave -D out/klipper.bin

dfu-util 0.9

Copyright 2005-2009 Weston Schmidt, Harald Welte and OpenMoko Inc.
Copyright 2010-2016 Tormod Volden and Stefan Schmidt
This program is Free Software and has ABSOLUTELY NO WARRANTY
Please report bugs to http://sourceforge.net/p/dfu-util/tickets/

dfu-util: Invalid DFU suffix signature
dfu-util: A valid DFU suffix will be required in a future dfu-util release!!!
Opening DFU capable USB device...
ID 0483:df11
Run-time device DFU version 011a
Claiming USB DFU Interface...
Setting Alternate Setting #0 ...
Determining device status: state = dfuIDLE, status = 0
dfuIDLE, continuing
DFU mode device DFU version 011a
Device returned transfer size 1024
DfuSe interface name: "Internal Flash   "
Downloading to address = 0x08000000, size = 30448
Download	[=========================] 100%        30448 bytes
Download done.
File downloaded successfully
dfu-util: Error during download get_status

Failed to flash to 0483:df11: Error running dfu-util

If the device is already in bootloader mode it can be flashed with the
following command:
  make flash FLASH_DEVICE=0483:df11
  OR
  make flash FLASH_DEVICE=1209:beba

If attempting to flash via 3.3V serial, then use:
  make serialflash FLASH_DEVICE=0483:df11

make: *** [src/stm32/Makefile:111: flash] Error 255

elizabeth-4, 2024-10-24:
the sensors are already plugged in

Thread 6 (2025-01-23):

Nevermore stealthmax pcb install issue

kenny00111, 2025-01-23:
Hi,
How should I install the PCB to the body. There is a mount (https://github.com/xbst/Nevermore-PCB/blob/master/Mounts/Stealthmax/Spacer.stl)in the repository but no idea how should it fit. If I just install normally the fan cable is just a few mm short to reach the connector.

Closed 2025-01-23.

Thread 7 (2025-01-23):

SM pcb fan never stops

kenny00111, 2025-01-23:
Hi the pwm fan never stops. It is always spinning around 1900rpm. It reacts to the pwm signal. Is it possible to turn it off completely?

xbst, 2025-01-24:
Below 20% PWM is not defined by the PWM speed control standard. Some fans turn off, some don't. Also, some Nevermore fans, especially ones sold on Aliexpress, don't actually work right. Their speed control is faulty.

kenny00111, 2025-01-30:
Hi. It worked perfectly (no spinning)for a few hours ( during sensor calibration). Now it's just erratic. I bought it from onetwo3d. It supposed to be a genuine delta fan. I connected directly to the PCB, all connections are ok.

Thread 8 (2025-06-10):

Random I2C NACK on SM2

Waranga-pa, 2025-06-10:
I randomly run into I2C NACK while printing (in opposite to ticket I2C Errors I randomly run into I2C NACK while printing (in opposite to ticket I2C Errors https://github.com/xbst/Nevermore-PCB/issues/4). I have jobs with 15+ hours without any issues but also fails after 30-45 minutes. Before the shutdown, everything looks fine, I get readouts on both BME280 and SGP40 modules, fan also works as expected. SM2 is connected via CANBUS, together with other modules but communication is perfect there with or without SM2. To me, it looks like I2C bus queue gets gridlocked. Beside fixing the error, is there an option to lower priority to not lead to a full shutdown and loss of the print?

klippy.log:
MCU 'stealthmax_2' shutdown: I2C NACK
clocksync state: mcu_freq=64000000 last_clock=803808385224 clock_est=(12522.476 801956530347 63999574.163) min_half_rtt=0.000126 min_rtt_time=11671.063 time_avg=12522.476(882.228) clock_avg=801956530347.340(56462212397.992) pred_variance=6223722.347 clock_adj=(-0.011 63999371.630)
Dumping serial stats: bytes_write=1057072 bytes_read=3101191 bytes_retransmit=0 bytes_invalid=0 send_seq=103934 receive_seq=103934 retransmit_seq=0 srtt=0.002 rttvar=0.001 rto=0.025 ready_bytes=0 upcoming_bytes=0
Dumping send queue 100 messages
Sent 0 12540.598652 12540.598434 16: seq: 1a, i2c_write oid=2 data=b'&\x0f\x18\xae;\x84\xf1\x92'
Sent 1 12540.617674 12540.617456 16: seq: 1b, i2c_write oid=3 data=b'&\x0f!\xf6\x8d\x80\xac#'
Sent 2 12540.649599 12540.649437 9: seq: 1c, i2c_read oid=2 reg=b'' read_len=3
Sent 3 12540.668831 12540.668669 9: seq: 1d, i2c_read oid=3 reg=b'' read_len=3
Sent 4 12540.792806 12540.792715 6: seq: 1e, get_canbus_status
Sent 5 12541.029036 12541.028866 10: seq: 1f, i2c_read oid=0 reg=b'\xf7' read_len=8
Sent 6 12541.029474 12541.029304 10: seq: 10, i2c_read oid=1 reg=b'\xf7' read_len=8
Sent 7 12541.564573 12541.564482 6: seq: 11, get_clock
Sent 8 12541.655190 12541.654972 16: seq: 12, i2c_write oid=2 data=b'&\x0f\x18\xa6\x82\x84\xf1\x92'
Sent 9 12541.674545 12541.674327 16: seq: 13, i2c_write oid=3 data=b'&\x0f!\xfa\xf0\x80\xb0\x1d'
Sent 10 12541.706455 12541.706293 9: seq: 14, i2c_read oid=2 reg=b'' read_len=3
Sent 11 12541.725947 12541.725785 9: seq: 15, i2c_read oid=3 reg=b'' read_len=3
Sent 12 12541.794746 12541.794655 6: seq: 16, get_canbus_status
Sent 13 12541.831976 12541.831806 10: seq: 17, i2c_read oid=0 reg=b'\xf7' read_len=8
Sent 14 12541.832876 12541.832706 10: seq: 18, i2c_read oid=1 reg=b'\xf7' read_len=8
Sent 15 12542.549097 12542.549006 6: seq: 19, get_clock
Sent 16 12542.634855 12542.634685 10: seq: 1a, i2c_read oid=0 reg=b'\xf7' read_len=8
Sent 17 12542.636646 12542.636476 10: seq: 1b, i2c_read oid=1 reg=b'\xf7' read_len=8
Sent 18 12542.711914 12542.711696 16: seq: 1c, i2c_write oid=2 data=b'&\x0f\x18\xb2\x05\x84\xf1\x92'
Sent 19 12542.729869 12542.729651 16: seq: 1d, i2c_write oid=3 data=b'&\x0f!\xfa\xf0\x80\xac#'
Sent 20 12542.762592 12542.762430 9: seq: 1e, i2c_read oid=2 reg=b'' read_len=3
Sent 21 12542.781169 12542.781007 9: seq: 1f, i2c_read oid=3 reg=b'' read_len=3
Sent 22 12542.796991 12542.796900 6: seq: 10, get_canbus_status
Sent 23 12543.438821 12543.438651 10: seq: 11, i2c_read oid=0 reg=b'\xf7' read_len=8
Sent 24 12543.439638 12543.439468 10: seq: 12, i2c_read oid=1 reg=b'\xf7' read_len=8
Sent 25 12543.534248 12543.534157 6: seq: 13, get_clock
Sent 26 12543.767802 12543.767584 16: seq: 14, i2c_write oid=2 data=b'&\x0f\x18\xb2\x05\x84\xf1\x92'
Sent 27 12543.785716 12543.785498 16: seq: 15, i2c_write oid=3 data=b'&\x0f!\xfe4\x80\xb0\x1d'
Sent 28 12543.798816 12543.798725 6: seq: 16, get_canbus_status
Sent 29 12543.818801 12543.818639 9: seq: 17, i2c_read oid=2 reg=b'' read_len=3
Sent 30 12543.836255 12543.836093 9: seq: 18, i2c_read oid=3 reg=b'' read_len=3
Sent 31 12544.243702 12544.243532 10: seq: 19, i2c_read oid=0 reg=b'\xf7' read_len=8
Sent 32 12544.244176 12544.244006 10: seq: 1a, i2c_read oid=1 reg=b'\xf7' read_len=8
Sent 33 12544.518458 12544.518367 6: seq: 1b, get_clock
Sent 34 12544.800856 12544.800765 6: seq: 1c, get_canbus_status
Sent 35 12544.823615 12544.823397 16: seq: 1d, i2c_write oid=2 data=b'&\x0f\x18\xae;\x84\xf1\x92'
Sent 36 12544.840391 12544.840173 16: seq: 1e, i2c_write oid=3 data=b'&\x0f!\xf6\x8d\x80\xb0\x1d'
Sent 37 12544.874510 12544.874348 9: seq: 1f, i2c_read oid=2 reg=b'' read_len=3
Sent 38 12544.891519 12544.891357 9: seq: 10, i2c_read oid=3 reg=b'' read_len=3
Sent 39 12545.048198 12545.048028 10: seq: 11, i2c_read oid=0 reg=b'\xf7' read_len=8
Sent 40 12545.048840 12545.048670 10: seq: 12, i2c_read oid=1 reg=b'\xf7' read_len=8
Sent 41 12545.503160 12545.503069 6: seq: 13, get_clock
Sent 42 12545.802398 12545.802307 6: seq: 14, get_canbus_status
Sent 43 12545.851115 12545.850945 10: seq: 15, i2c_read oid=0 reg=b'\xf7' read_len=8
Sent 44 12545.853616 12545.853446 10: seq: 16, i2c_read oid=1 reg=b'\xf7' read_len=8
Sent 45 12545.879467 12545.879249 16: seq: 17, i2c_write oid=2 data=b'&\x0f\x18\xa2F\x84\xf1\x92'
Sent 46 12545.895807 12545.895589 16: seq: 18, i2c_write oid=3 data=b'&\x0f!\xf1\x1a\x80\xb0\x1d'
Sent 47 12545.930747 12545.930585 9: seq: 19, i2c_read oid=2 reg=b'' read_len=3
Sent 48 12545.946827 12545.946665 9: seq: 1a, i2c_read oid=3 reg=b'' read_len=3
Sent 49 12546.487795 12546.487704 6: seq: 1b, get_clock
Sent 50 12546.655476 12546.655306 10: seq: 1c, i2c_read oid=0 reg=b'\xf7' read_len=8
Sent 51 12546.657624 12546.657454 10: seq: 1d, i2c_read oid=1 reg=b'\xf7' read_len=8
Sent 52 12546.804766 12546.804675 6: seq: 1e, get_canbus_status
Sent 53 12546.937811 12546.937593 16: seq: 1f, i2c_write oid=2 data=b'&\x0f\x18\xae;\x84\xf1\x92'
Sent 54 12546.951636 12546.951418 16: seq: 10, i2c_write oid=3 data=b'&\x0f!\xf5\xde\x80\xb0\x1d'
Sent 55 12546.989314 12546.989152 9: seq: 11, i2c_read oid=2 reg=b'' read_len=3
Sent 56 12547.002509 12547.002347 9: seq: 12, i2c_read oid=3 reg=b'' read_len=3
Sent 57 12547.459029 12547.458859 10: seq: 13, i2c_read oid=0 reg=b'\xf7' read_len=8
Sent 58 12547.461255 12547.461085 10: seq: 14, i2c_read oid=1 reg=b'\xf7' read_len=8
Sent 59 12547.472177 12547.472086 6: seq: 15, get_clock
Sent 60 12547.806885 12547.806794 6: seq: 16, get_canbus_status
Sent 61 12547.994073 12547.993855 16: seq: 17, i2c_write oid=2 data=b'&\x0f\x18\xaa\xff\x84\xee\xff'
Sent 62 12548.006908 12548.006690 16: seq: 18, i2c_write oid=3 data=b'&\x0f!\xf1\x1a\x80\xb0\x1d'
Sent 63 12548.044677 12548.044515 9: seq: 19, i2c_read oid=2 reg=b'' read_len=3
Sent 64 12548.058293 12548.058131 9: seq: 1a, i2c_read oid=3 reg=b'' read_len=3
Sent 65 12548.263010 12548.262840 10: seq: 1b, i2c_read oid=0 reg=b'\xf7' read_len=8
Sent 66 12548.264735 12548.264565 10: seq: 1c, i2c_read oid=1 reg=b'\xf7' read_len=8
Sent 67 12548.457257 12548.457166 6: seq: 1d, get_clock
Sent 68 12548.808518 12548.808427 6: seq: 1e, get_canbus_status
Sent 69 12549.049756 12549.049538 16: seq: 1f, i2c_write oid=2 data=b'&\x0f\x18\x9e\xfe\x84\xf1\x92'
Sent 70 12549.062744 12549.062526 16: seq: 10, i2c_write oid=3 data=b'&\x0f!\xf5\xde\x80\xb0\x1d'
Sent 71 12549.066215 12549.066045 10: seq: 11, i2c_read oid=0 reg=b'\xf7' read_len=8
Sent 72 12549.067683 12549.067513 10: seq: 12, i2c_read oid=1 reg=b'\xf7' read_len=8
Sent 73 12549.100308 12549.100146 9: seq: 13, i2c_read oid=2 reg=b'' read_len=3
Sent 74 12549.113973 12549.113811 9: seq: 14, i2c_read oid=3 reg=b'' read_len=3
Sent 75 12549.441925 12549.441834 6: seq: 15, get_clock
Sent 76 12549.810210 12549.810119 6: seq: 16, get_canbus_status
Sent 77 12549.869676 12549.869506 10: seq: 17, i2c_read oid=0 reg=b'\xf7' read_len=8
Sent 78 12549.870215 12549.870045 10: seq: 18, i2c_read oid=1 reg=b'\xf7' read_len=8
Sent 79 12550.104578 12550.104360 16: seq: 19, i2c_write oid=2 data=b'&\x0f\x18\x9e\xfe\x84\xf1\x92'
Sent 80 12550.118144 12550.117926 16: seq: 1a, i2c_write oid=3 data=b'&\x0f!\xf1\x1a\x80\xb0\x1d'
Sent 81 12550.155828 12550.155666 9: seq: 1b, i2c_read oid=2 reg=b'' read_len=3
Sent 82 12550.168407 12550.168245 9: seq: 1c, i2c_read oid=3 reg=b'' read_len=3
Sent 83 12550.426701 12550.426610 6: seq: 1d, get_clock
Sent 84 12550.674062 12550.673892 10: seq: 1e, i2c_read oid=0 reg=b'\xf7' read_len=8
Sent 85 12550.674397 12550.674227 10: seq: 1f, i2c_read oid=1 reg=b'\xf7' read_len=8
Sent 86 12550.811938 12550.811847 6: seq: 10, get_canbus_status
Sent 87 12551.162014 12551.161796 16: seq: 11, i2c_write oid=2 data=b'&\x0f\x18\xa2F\x84\xf1\x92'
Sent 88 12551.172972 12551.172754 16: seq: 12, i2c_write oid=3 data=b'&\x0f!\xf5\xde\x80\xb0\x1d'
Sent 89 12551.212766 12551.212604 9: seq: 13, i2c_read oid=2 reg=b'' read_len=3
Sent 90 12551.224137 12551.223975 9: seq: 14, i2c_read oid=3 reg=b'' read_len=3
Sent 91 12551.411102 12551.411011 6: seq: 15, get_clock
Sent 92 12551.477874 12551.477704 10: seq: 16, i2c_read oid=0 reg=b'\xf7' read_len=8
Sent 93 12551.478324 12551.478154 10: seq: 17, i2c_read oid=1 reg=b'\xf7' read_len=8
Sent 94 12551.814334 12551.814243 6: seq: 18, get_canbus_status
Sent 95 12552.217943 12552.217725 16: seq: 19, i2c_write oid=2 data=b'&\x0f\x18\xa2F\x84\xf1\x92'
Sent 96 12552.228540 12552.228322 16: seq: 1a, i2c_write oid=3 data=b'&\x0f!\xf1\x1a\x80\xb3N'
Sent 97 12552.269034 12552.268872 9: seq: 1b, i2c_read oid=2 reg=b'' read_len=3
Sent 98 12552.285216 12552.284927 19: seq: 1c, i2c_read oid=0 reg=b'\xf7' read_len=8, i2c_read oid=1 reg=b'\xf7' read_len=8, i2c_read oid=3 reg=b'' read_len=3
Sent 99 12552.303259 12552.303097 9: seq: 1d, i2c_read oid=3 reg=b'' read_len=3
Dumping receive queue 100 messages
Receive: 0 12545.471033 12545.048840 15: seq: 13, analog_in_state oid=6 next_clock=288063855 value=29888
Receive: 1 12545.481043 12545.048840 14: seq: 13, analog_in_state oid=7 next_clock=288703855 value=7885
Receive: 2 12545.503526 12545.503160 11: seq: 14, clock clock=271394576
Receive: 3 12545.771059 12545.503160 15: seq: 14, analog_in_state oid=6 next_clock=307263855 value=29872
Receive: 4 12545.781063 12545.503160 14: seq: 14, analog_in_state oid=7 next_clock=307903855 value=7887
Receive: 5 12545.802793 12545.802398 11: seq: 15, canbus_status rx_error=0 tx_error=0 tx_retries=0 canbus_bus_state=active
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

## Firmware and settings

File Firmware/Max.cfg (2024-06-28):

[sgp40]

[mcu max]
# Uncomment "serial" if using USB, uncomment "canbus_uuid" if using CAN. Edit the serial address or UUID with the correct address/UUID for your PCB.

# serial: /dev/serial/by-id/usb-Klipper_stm32g0b1xx_000000000000000000000000-if00 # < update with the correct serial address
# canbus_uuid: 123456789012 # < update with the correct CAN Bus UUID

# Edit the I2C bus to match which sensors are connected to which connector on the PCB.
# Below is configured for BOTH air intake sensors wired to I2C1 (AKA SENSORS1 on the PCB),
# and BOTH exhaust sensors are wired to I2C2 (AKA SENSORS2 on the PCB).

# i2c_bus        | Connector
# i2c1_PB8_PB9   | SENSORS1
# i2c2_PB10_PB11 | SENSORS2

[temperature_sensor BME_OUT]
sensor_type: BME280
i2c_address: 119
i2c_mcu: max
i2c_bus: i2c1_PB8_PB9

[temperature_sensor BME_IN]
sensor_type: BME280
i2c_address: 119
i2c_mcu: max
i2c_bus: i2c2_PB10_PB11

[temperature_sensor SGP_OUT]
sensor_type: SGP40
i2c_mcu: max
i2c_bus: i2c1_PB8_PB9
ref_temp_sensor: bme280 BME_OUT
ref_humidity_sensor: bme280 BME_OUT

[temperature_sensor SGP_IN]
sensor_type: SGP40
i2c_mcu: max
i2c_bus: i2c2_PB10_PB11
ref_temp_sensor: bme280 BME_IN
ref_humidity_sensor: bme280 BME_IN

[fan_generic Filter]
pin: max:PB14
tachometer_pin: max:PB15
tachometer_ppr: 2

# Uncomment below if using the Max PCB AND want to use the 3-pin fan header

# [fan_generic Nevermore_Aux]
# pin: max:PA1
# tachometer_pin: max:PA0
# tachometer_ppr: 2

[neopixel Nevermore_LED]
pin: max:PD3
chain_count: 16
color_order: GRB
initial_RED: 1
initial_GREEN: 0
initial_BLUE: 0

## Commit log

2023-03-17 PCB Tray STL & PCB CAD Model
2023-10-21 SM PCB
    [BOM.csv, PNP.csv]
2024-06-23 Update and rename max.cfg to Max.cfg
    [Max.cfg]
2024-06-25 Fix PCB-Tray.stl
2024-06-28 SM2 mounts
    [Latch.stl, Spacer.stl, Stealthmax-Latch.step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]
2024-06-30 SM2 PCB Source
    [BOM.csv, PNP.csv]
